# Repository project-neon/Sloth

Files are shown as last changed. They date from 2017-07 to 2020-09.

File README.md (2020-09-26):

# Sloth
The Neon's Line Follower Robot of 2017
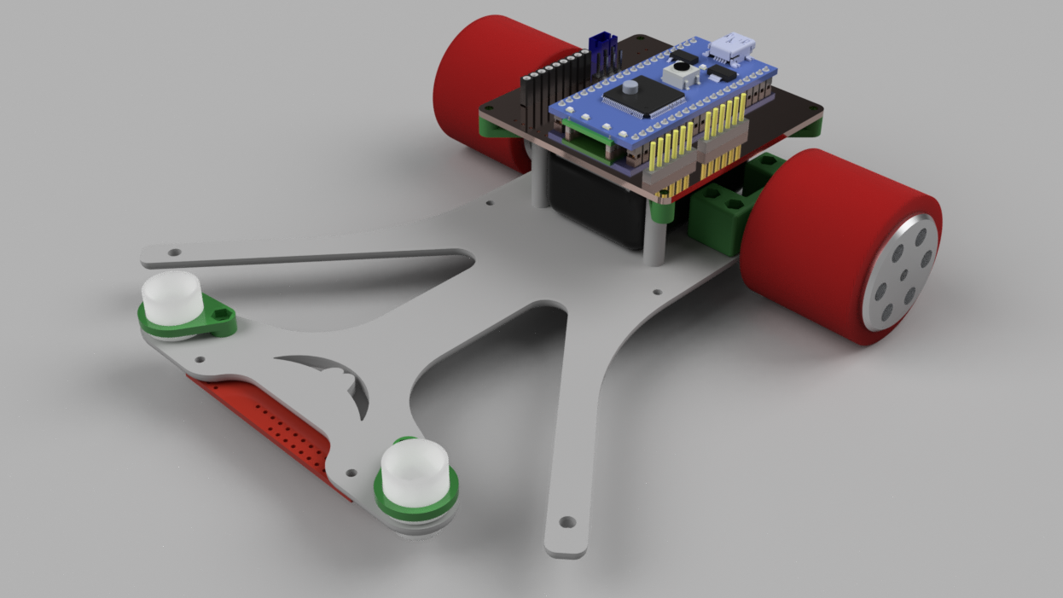
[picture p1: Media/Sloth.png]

<p align="center";> <b>The <strike>slowest</strike> fastest line follower in the ice age.</b> </p>

# Parts of the puzzle
* `Firmware`: Is the main firmware that controls all the functions of the robot.
* `Software`: Is telemetry software for data acquisition from the robot.
* `Eletronics`: This keeps all the information about the electronics for the line following robot ‘NoFollow’.
* `Mechanics`: Contains the STL files of the robot design.

## Firmware
The firmware project was based on the [mbed](https://developer.mbed.org/) development platform and was developed in the [Atom Text Editor](https://atom.io/) equipped with the [Platformio Extension](http://docs.platformio.org/en/latest/ide/atom.html).

### Firmware parts overview
* `main`: Controls all functions of the robot.
* `lineReader`: Read the outside sensors and check the conditions.
* `Motor`: Library for control the power and direction of the motors.
* `PID`: Configures PID control on the angular velocity of the robot.
* `QEI`: Libary for read the magnetic encoders. Available [here](https://developer.mbed.org/cookbook/QEI)
* `QTRSensors`: Library for read the line sensors. Available [here](https://developer.mbed.org/users/phillippsm/code/PololuQTRSensors/).

## Eletronics
The eletronic board was developed in the [Circuit Maker](https://circuitmaker.com/), a PCB Design Freeware. Project available [here](https://circuitmaker.com/Projects/Details/Neon-Project/NeoFollow).

### Bill of materials
| Qtd | Item | Buy | US$ |
|-----|---|-----|-----|
| 1 | ARM mbed NXP LPC1768 Development Board | [World](https://www.pololu.com/product/2150) | 49.00 | 
| 1 | QTR-8A Reflectance Sensor Array | [World](https://www.pololu.com/product/960) | 9.95 | 
| 1 | TB6612FNG Dual Motor Driver Carrier | [World](https://www.pololu.com/product/713) | 4.95 | 
| 1 | Bluetooth Module HC-05 | [World](https://www.robocore.net/loja/produtos/modulo-bluetooth-hc-05.html) | 12.30 | 
| 2 | 30:1 Micro Metal Gearmotor HP 6V with Extended Motor Shaft | [World](https://www.pololu.com/product/2212) | 16.95 | 
| 1 | Magnetic Encoder Pair Kit for Micro Metal Gearmotors | [World](https://www.pololu.com/product/3081) | 8.95 | 
| 1 | Profuse 2S 7.4V 850 Mah LiPo Battery | [World](http://www.jsumo.com/profuse-2s-74v-850-mah-lipo-battery) | 13.50 | 

## Mecanichs
The mechanics project was developed in the [Fusion 360](https://www.autodesk.com/products/fusion-360/overview), a 3D CAD/CAM Software free for students. Project available [here](http://a360.co/2tWd5yP).

### 3D Printed Parts
| Qtd | Item | 
|-----|---|
| 1 | Chassis |
| 4 | Motor Support |
| 2 | Ball Caster Holder |
| 3 | Spacer |
| 1 | PCB Support |

### Bill of materials
| Qtd | Item | Buy | US$ |
|-----|---|-----|-----|
| 1 | Atom Wheel 37x34mm Pair | [World](http://www.jsumo.com/atom-wheel-37x34mm-pair) | 19.50 | 
| 1 | Mini Plastic Caster Wheel Pair | [World](http://www.jsumo.com/mini-plastic-caster-wheel-pair) | 1.40 | 

## Software
Only a concept.

# Contributors
* [Gustavo Silva de Paula](https://github.com/gustavosdepaula)
* [Marcelo Farias](https://github.com/marcelojrfarias)

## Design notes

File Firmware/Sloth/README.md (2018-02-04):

# Sloth
This are the Firmwares used in the Winter Challenge XIII.

Using encoders to map the track to obtain maximum speed on the straight lines and differents PID constants.

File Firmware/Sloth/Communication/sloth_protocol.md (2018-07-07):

# Protocolo de configuração do Sloth

## Estrutura base de comandos

Os comandos podem ter basicamente 5 componentes essenciais, listados abaixo

| Length | Command | Status | Payload | CRC|
| --- | ---  | --- | --- | -- |

- Length: Tamanho do pacote, assim sabemos quantos bytes devemos esperar na serial. É importante considerar que os bytes não chegarão de uma só vez.
- Command: O comando que será recebido e processado
- Status: O status é aplicável à resposta ao comando. É bom ter um ACK pra ter certeza que um comando foi recebido. Mas é dispensável, podemos fazer uma comunicação malha aberta
- Payload: Quando aplicável, o comando poderá possuir um payload, que são dados necessários para o funcionamento do comando (e.g. definição de um valor)
- CRC: Falhas de comunicação acontecem. Esse campo é dispensável a priori, mas talvez a gente precise caso a comunicação esteja muito ruim.

## Lista de comandos

|Comando | OPCODE | TAG| Descrição|
| -----  | --- | --- | --- |
| Increment | 0x21 | SLOTH_OPCODE_INC | Incrementa uma variável utilizada no controle (KP, KI, KD, etc) |
| Decrement | 0x22 | SLOTH_OPCODE_DEC | Decrementa a mesma coisa|
| Set | 0x23 | SLOTH_OPCODE_SET | Define um valor específico para as variáveis utilizadas no controle |
| Full config | 0x24 | SLOTH_OPCODE_CONFIG | Define um conjunto de valores: kp, ki e kd ao mesmo tempo |
| Start | 0x25 | SLOTH_OPCODE_START | Inicia algum ciclo no robô |
| Stop | 0x26 | SLOTH_OPCODE_STOP | Para o que o robô está fazendo |
| Save | 0x27 | SLOTH_OPCODE_SAVE | Salva os parâmetros do PID na EEPROM |

## Definições de Payloads

### Sloth Control Var

Os comandos: Increment, Decrement e Set possuem um payload determinado "variable", uma estrutura de dados que possui um código pra variável e um valor, que define qual variável ele irá modificar. Atualmente, há uma lista com as seguintes variáveis identificadas na lista a seguir:

| Variável | Código | Tag |
| ---  |  ----- | --- |
| KP 	| 0x21 | SLOT_VAR_KP |
| KI 	| 0x22 | SLOT_VAR_KI |
| KD 	| 0x23 | SLOT_VAR_KD |

Exemplos de comandos codificados

| Comando | Byte array | obs|
| ---- | ---- | -- |
| Inc KP | 0x02 0x21 0x21 | Observe que o campo "value" não é preenchido/transmitido |
| Dec KP | 0x02 0x22 0x21 | Observe que o campo "value" não é preenchido/transmitido |
| Dec KD | 0x02 0x22 0x23 | Observe que o campo "value" não é preenchido/transmitido |
| Set KI | 0x06 0x23 0x22 0x00 0x00 0x25 0x31 | Depois temos que ver como fica o endian disso aqui! |
| Set KD | 0x06 0x23 0x23 0x00 0x00 0x02 0x15 | Depois temos que ver como fica o endian disso aqui! |

### Config

O comando de configuração receve uma estrutura de dados do tipo "slot_config_t" que possui valores definidos para kp, ki e kd.

### Exemplo
Os comandos Increment e Decrement podem possuir o seguinte payload: KP, KI ou KD. Numa "metalinguagem" o comando ficaria algo do tipo (excluindo crc):

Requisição:

|2 | Increment | KP |
| -----  | --- | --- |

Resposta:

|2 | Increment | SUCCESS |
| -----  | --- | --- |

O comando Set poderia ter um conjunto de argumentos:

Requisição:

|4 | Set | KP Value | KI Value | KD Value |
| -----  | -- | ---- | --- | --- |

Resposta:

|2 | Set | SUCCESS |
| -----  | --- | --- |

No caso, tudo que vem depois do SET é o payload do comando.

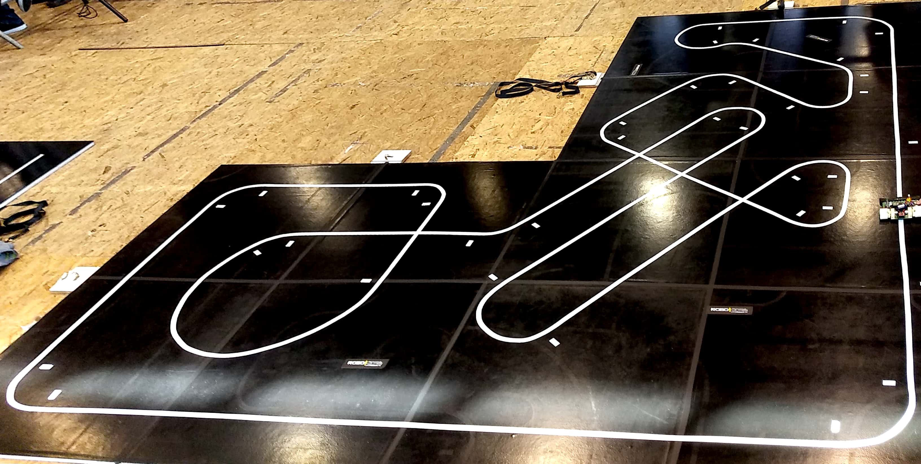
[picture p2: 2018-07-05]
Media/WC14.jpg

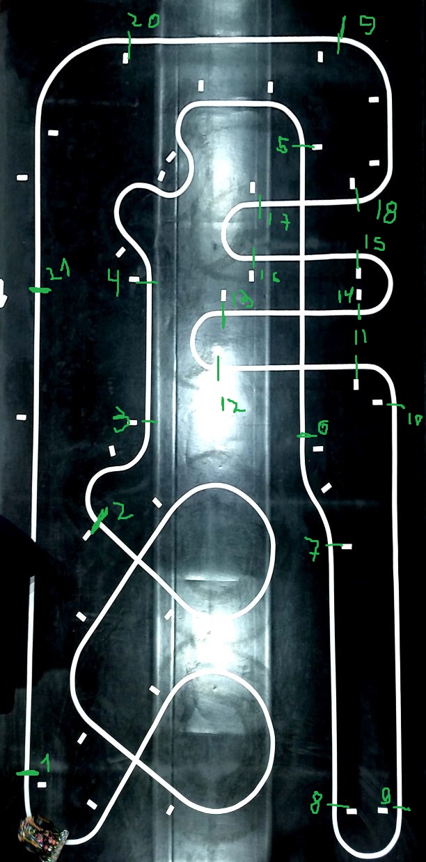
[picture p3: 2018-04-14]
Media/IronCup2018 - Marked.jpg

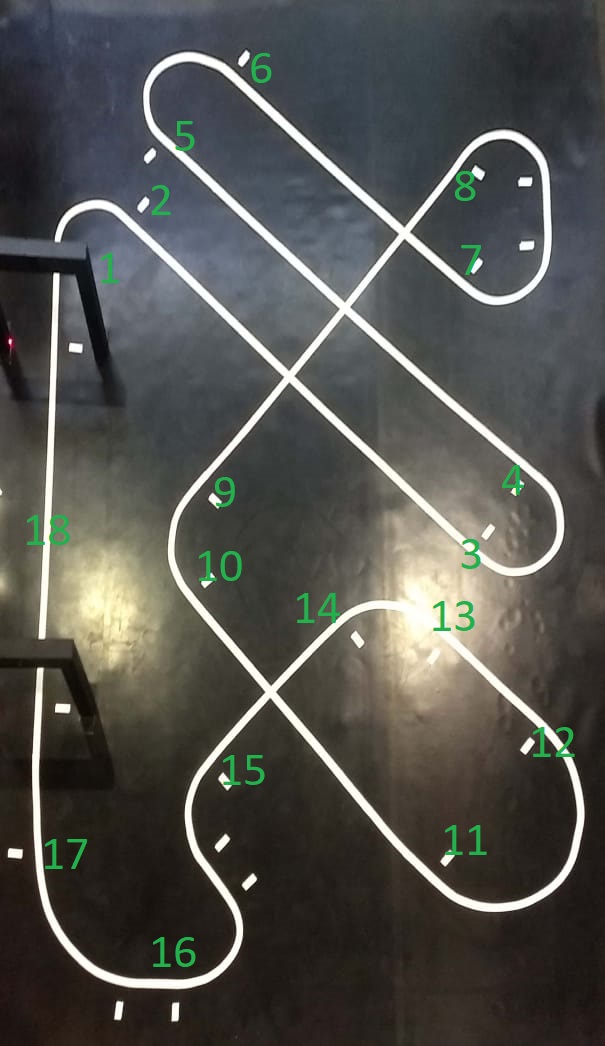
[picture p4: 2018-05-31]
Media/Smile2018 -marked.jpeg

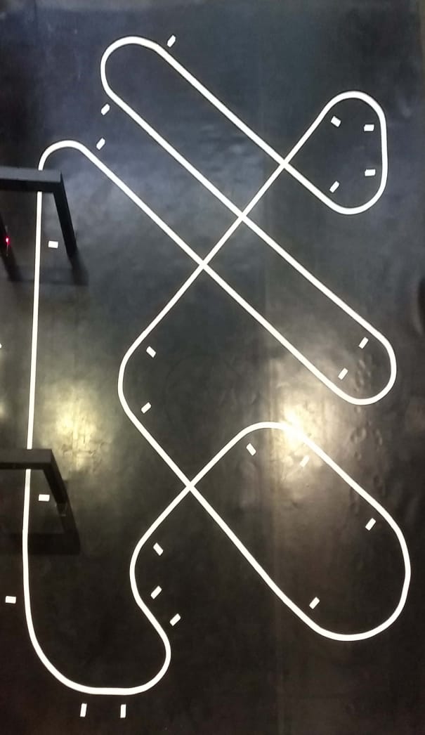
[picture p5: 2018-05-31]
Media/Smile2018.jpeg

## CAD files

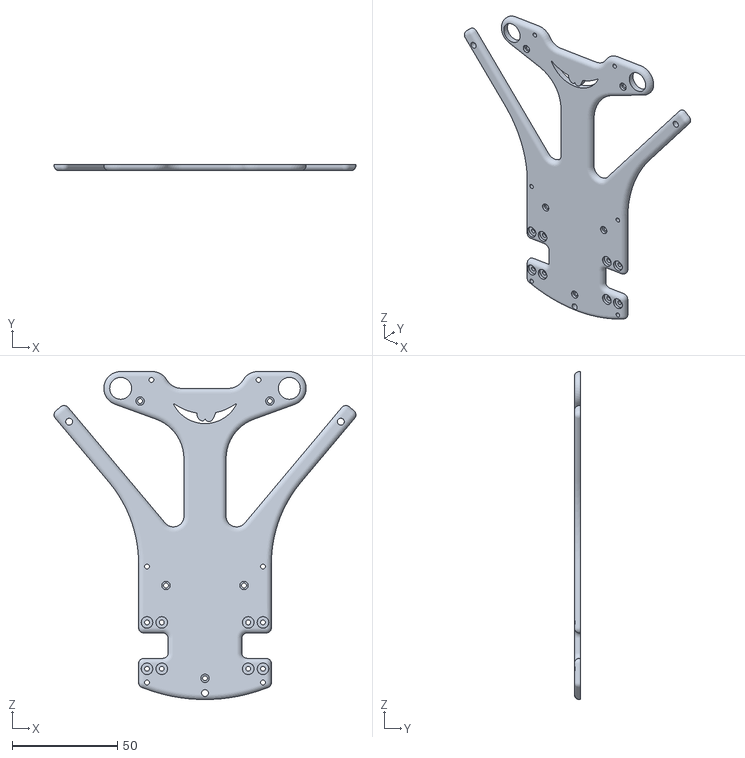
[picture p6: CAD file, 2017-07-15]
Mechanics/STL Files/1x Chassi v26.stl
143.2 x 3.00 x 155.6

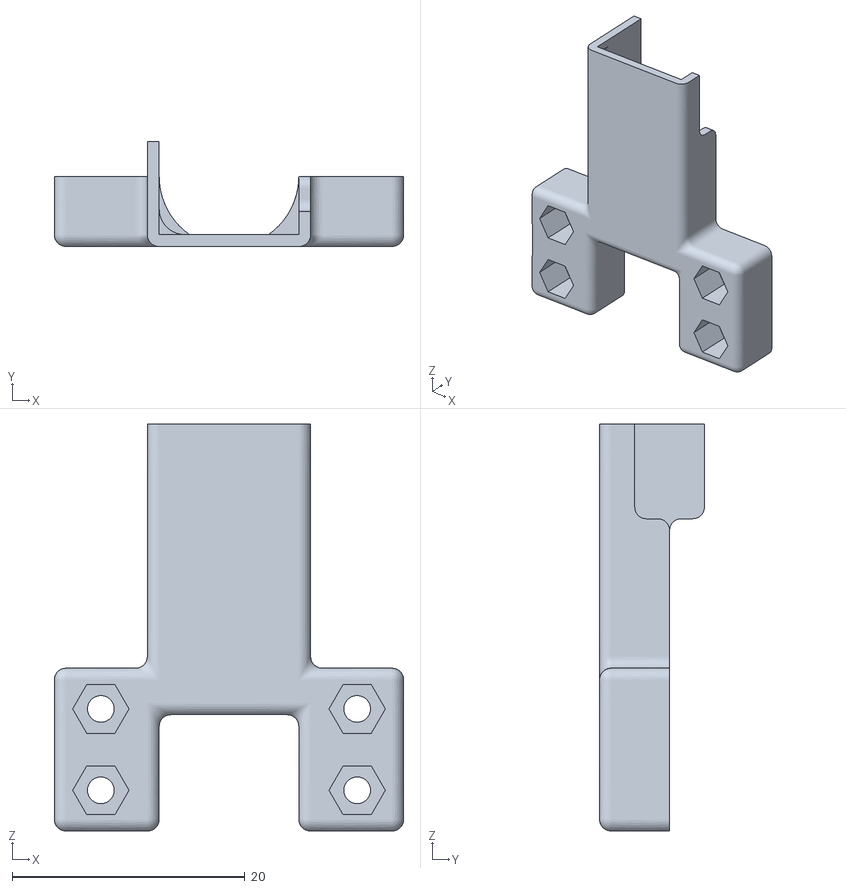
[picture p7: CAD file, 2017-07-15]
Mechanics/STL Files/4x Motor Support v5.stl
30.0 x 9.02 x 35.0

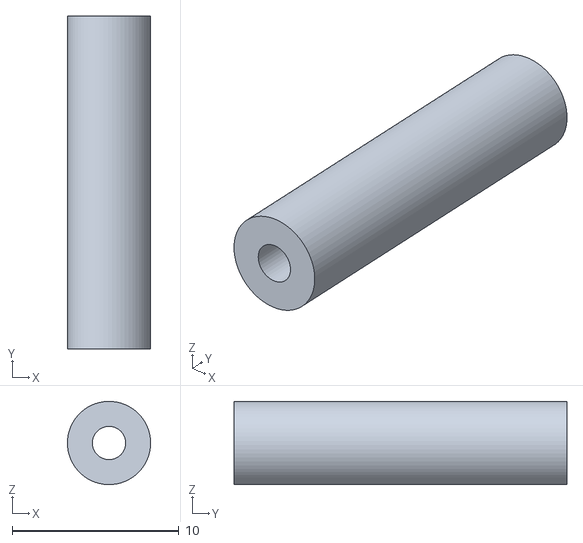
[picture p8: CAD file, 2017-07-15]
Mechanics/STL Files/3x Spacer v7.stl
5.00 x 20.0 x 5.00

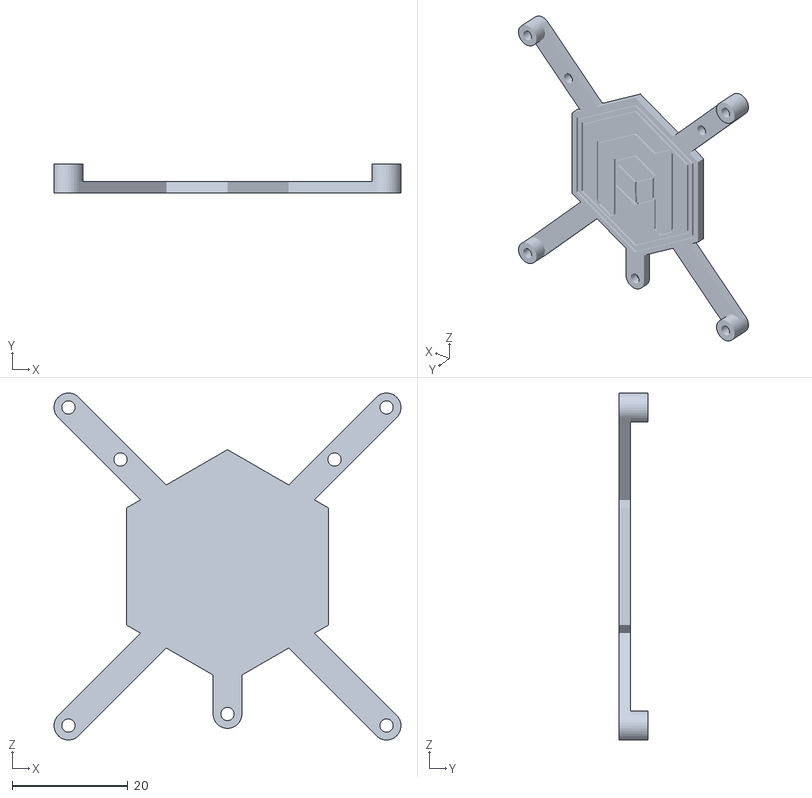
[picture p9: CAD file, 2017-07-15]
Mechanics/STL Files/1x PCBSupport v3.stl
60.0 x 5.00 x 60.0

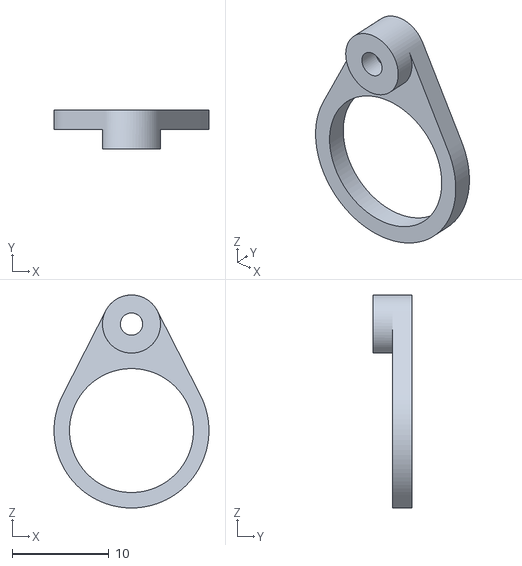
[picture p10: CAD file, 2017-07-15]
Mechanics/STL Files/2x BallCasterHolder v6.stl
16.0 x 4.00 x 22.0

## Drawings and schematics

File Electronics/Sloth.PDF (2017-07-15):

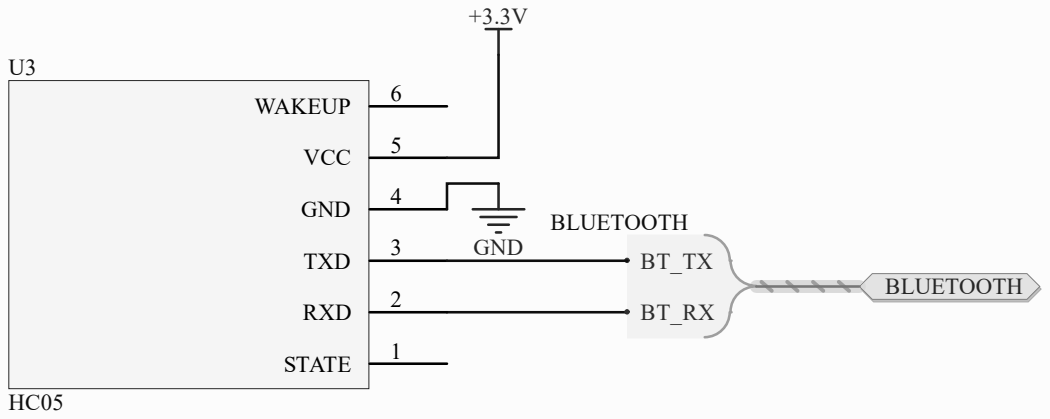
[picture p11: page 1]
POBLUETOOTH0BT0RX POBLUETOOTH0BT0TX

Size A | Number | Revision

Date: 15-Jul-17 | Sheet of
File: Communcation.SchDoc | Drawn By:

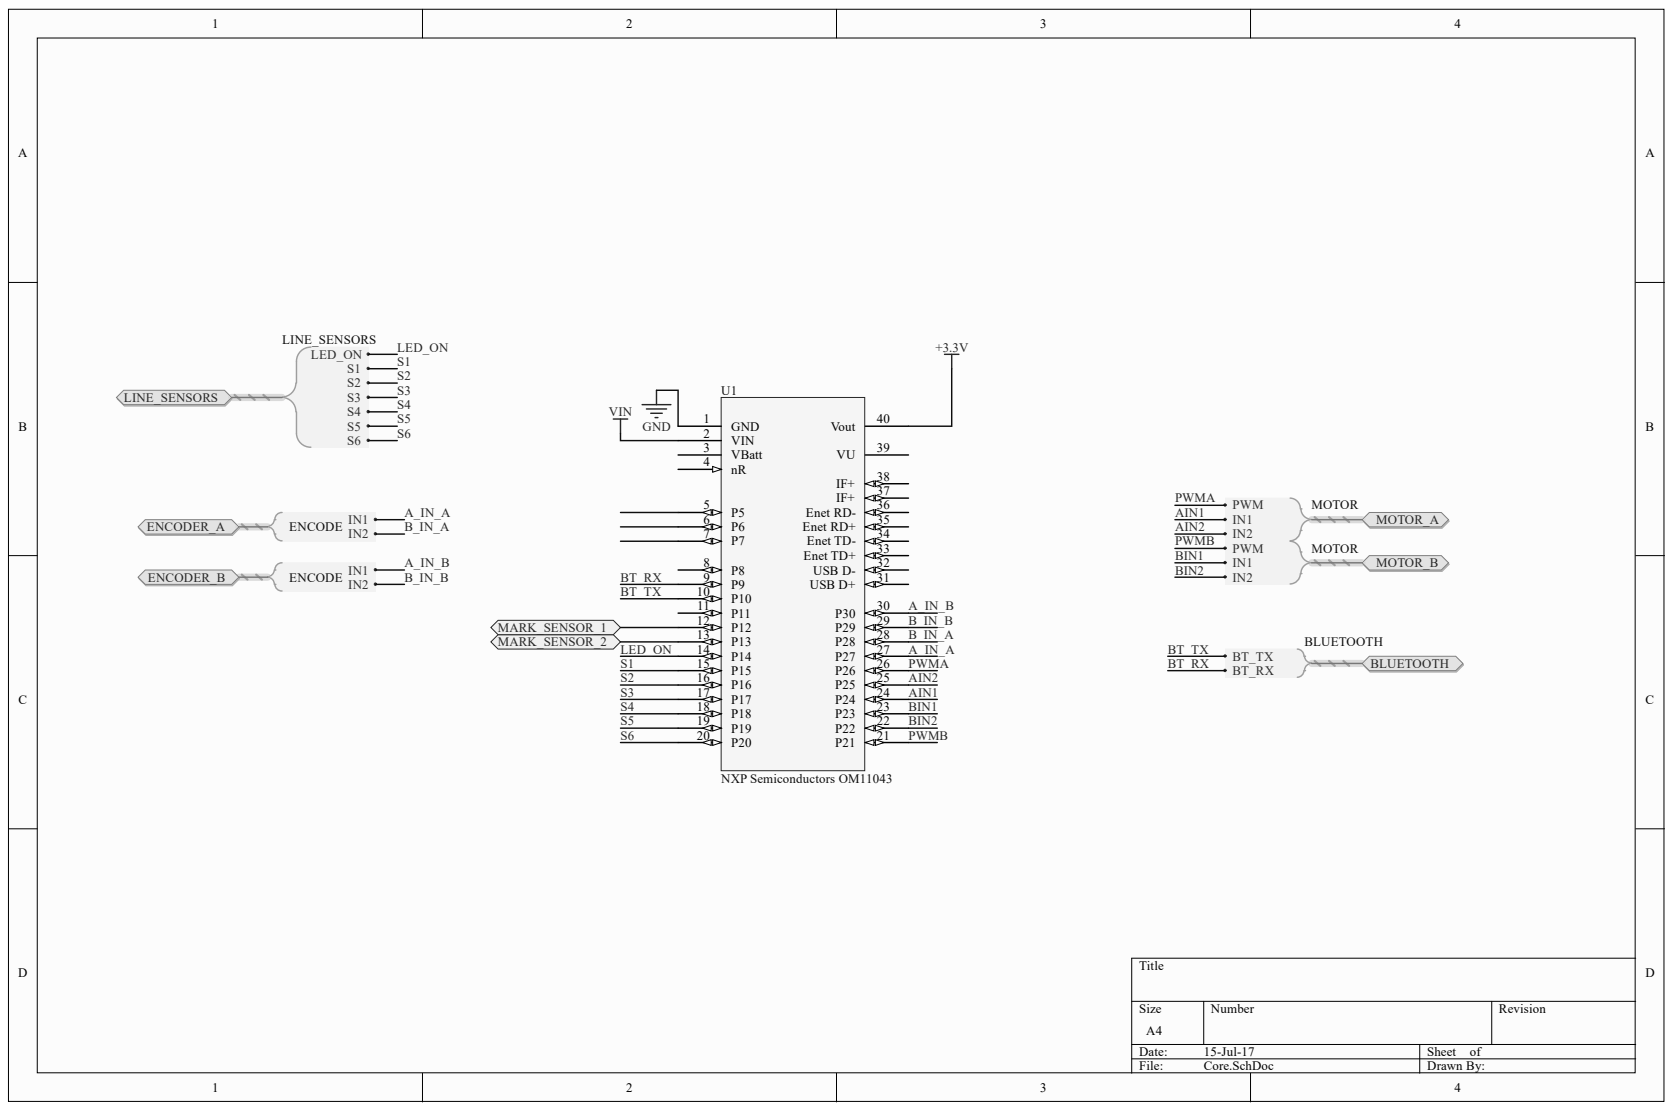
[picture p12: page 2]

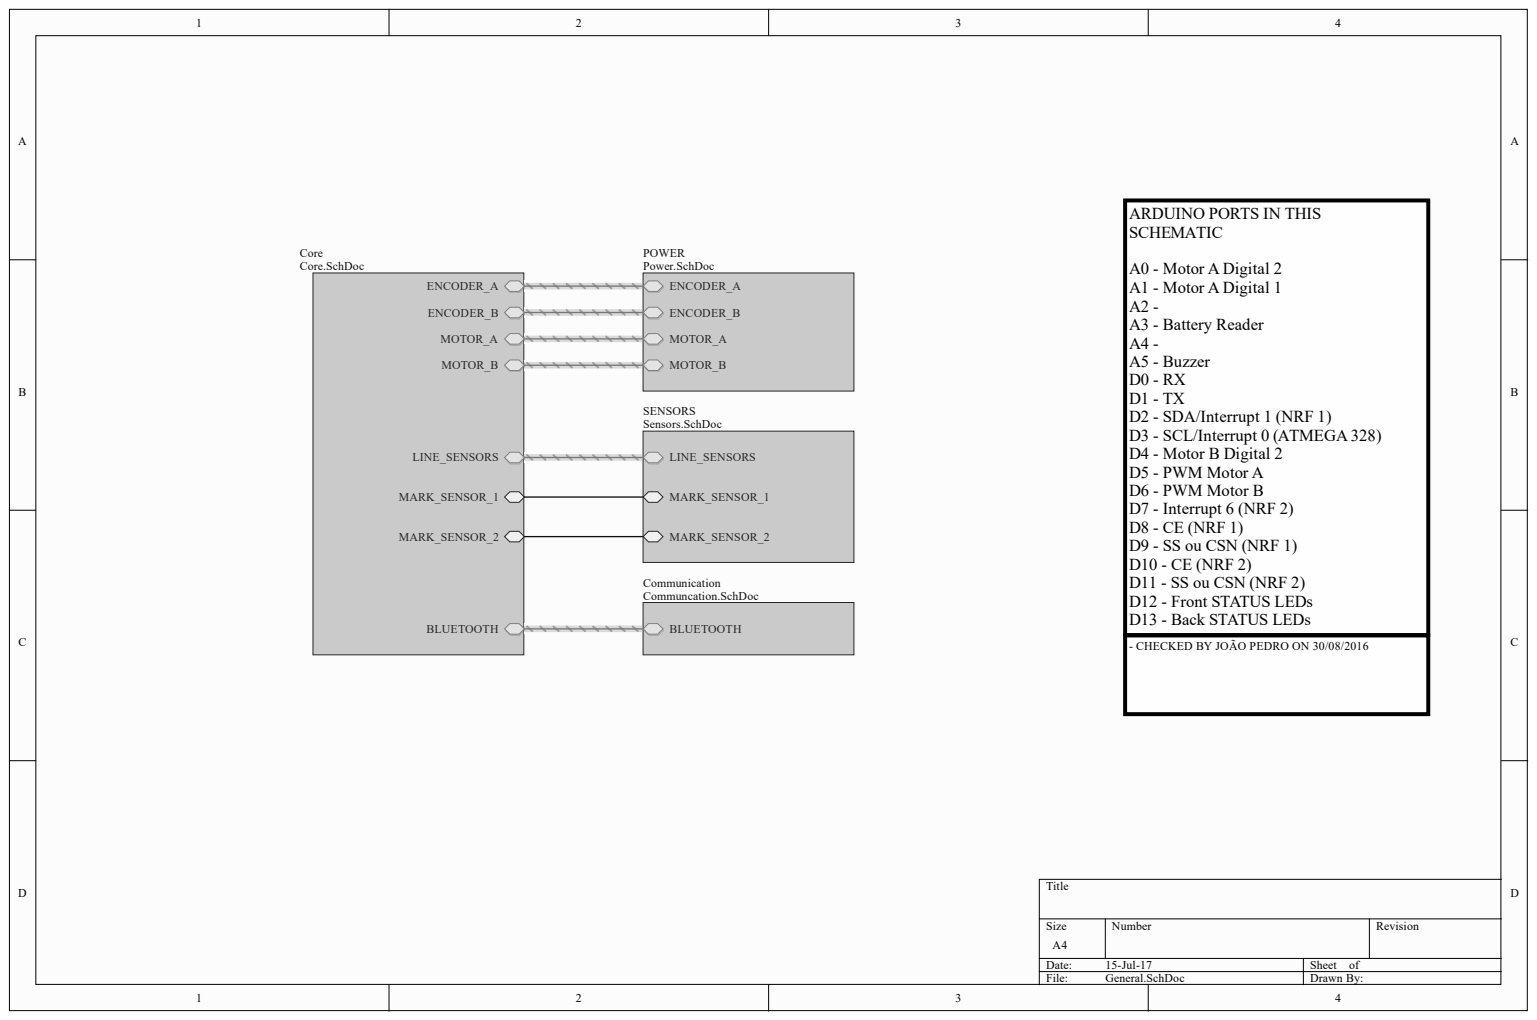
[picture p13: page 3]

ARDUINO PORTS IN THIS
SCHEMATIC

A0 - Motor A Digital 2
A1 - Motor A Digital 1
A3 - Battery Reader
A5 - Buzzer
D2 - SDA/Interrupt 1 (NRF 1)
D3 - SCL/Interrupt 0 (ATMEGA 328)
D4 - Motor B Digital 2
D5 - PWM Motor A
D6 - PWM Motor B
D7 - Interrupt 6 (NRF 2)
D8 - CE (NRF 1)
D9 - SS ou CSN (NRF 1)
D10 - CE (NRF 2)
D11 - SS ou CSN (NRF 2)
D12 - Front STATUS LEDs
D13 - Back STATUS LEDs

- CHECKED BY JOÃO PEDRO ON 30/08/2016

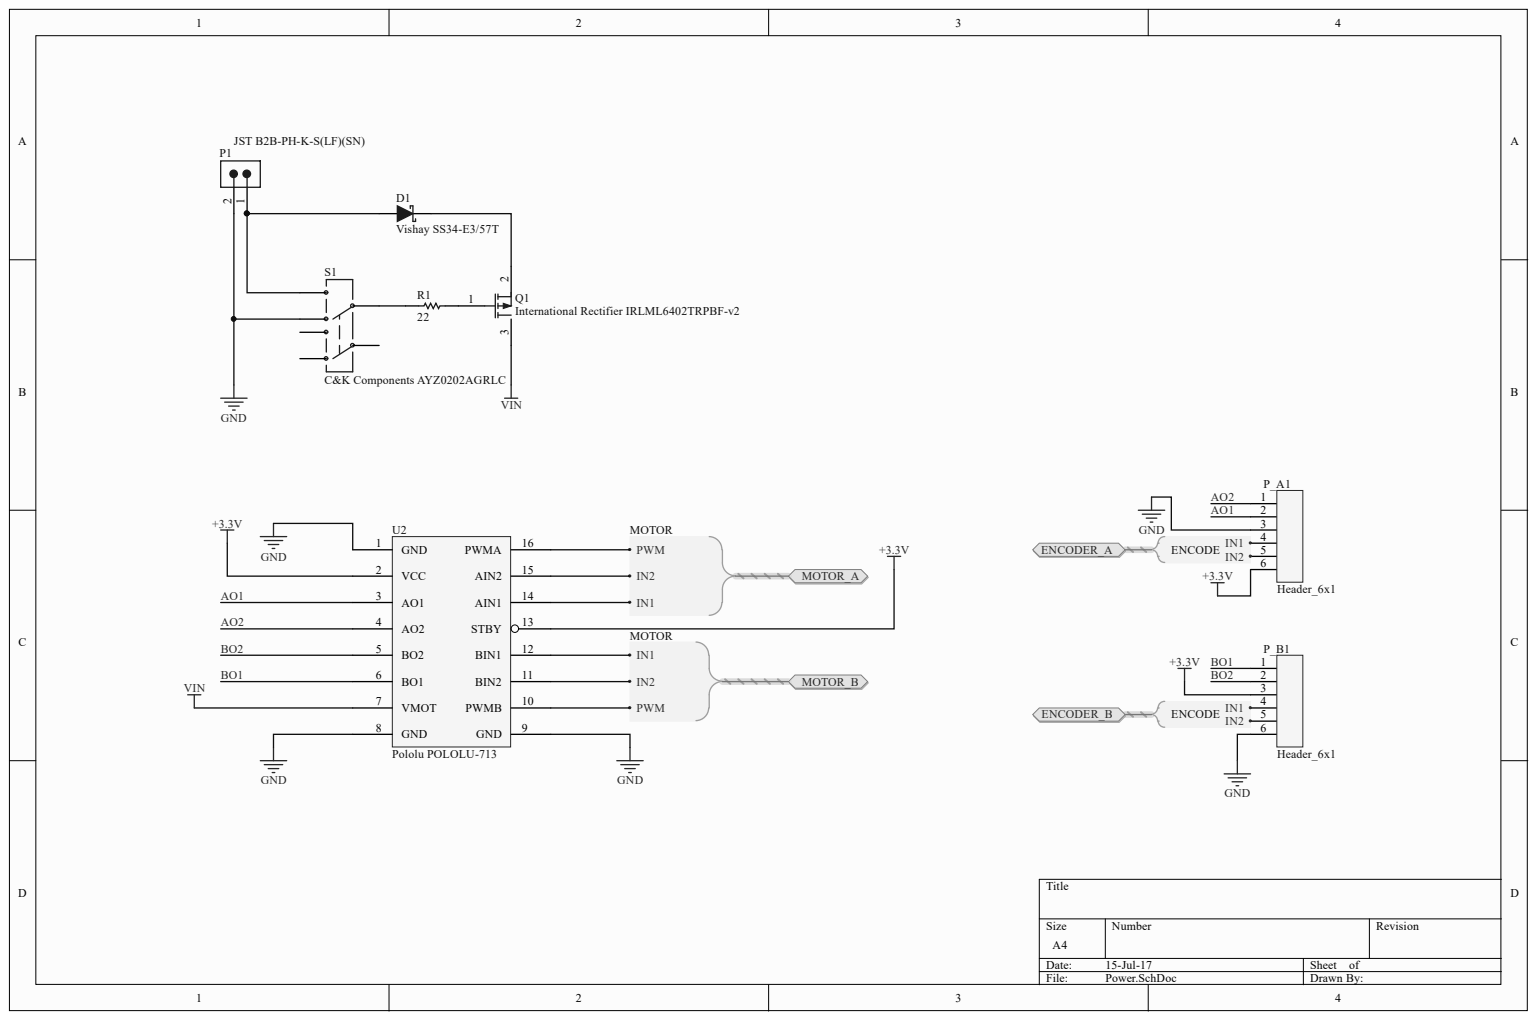
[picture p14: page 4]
File:; Power.SchDoc; Drawn By:; GND 1; VCC 2; VMOT 7; GND 8; GND; Pololu POLOLU-713; C&K Components AYZ0202AGRLC; International Rectifier IRLML6402TRPBF-v2; Vishay SS34-E3/57T; IN1 ENCODE; IN1 ENCODER_B; ENCODE

JST B2B-PH-K-S(LF)(SN)

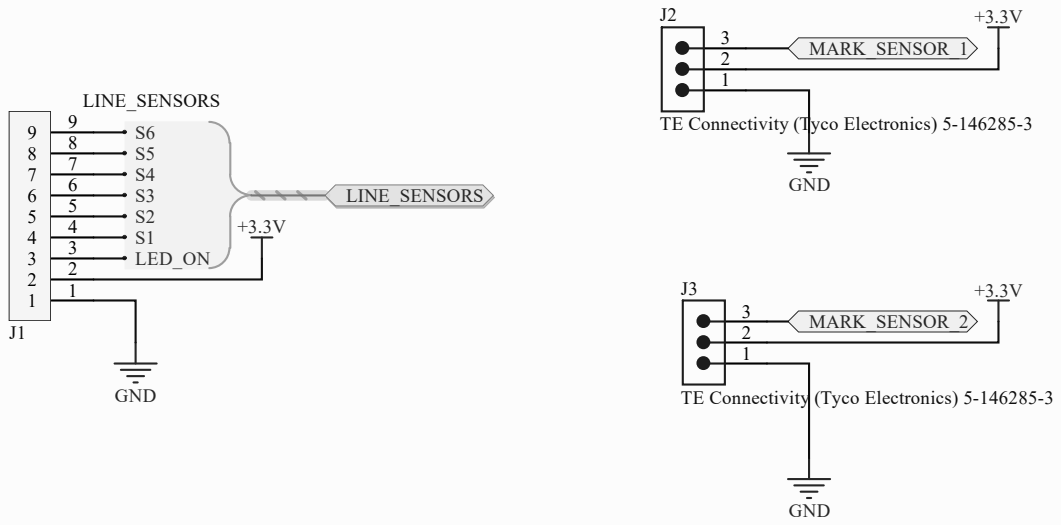
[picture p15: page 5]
File:; Sensors.SchDoc; Drawn By:; TE Connectivity (Tyco Electronics) 5-146285-3; COJ3 PIJ102; PIJ303 POMARK0SENSOR02; POLINE0SENSORS0LED0ON POLINE0SENSORS0S1 POLINE0SENSORS0S2 POLINE0SENSORS0S3 POLINE0SENSORS0S4 POLINE0SENSORS0S5 POLINE0SENSORS0S6

TE Connectivity (Tyco Electronics) 5-146285-3

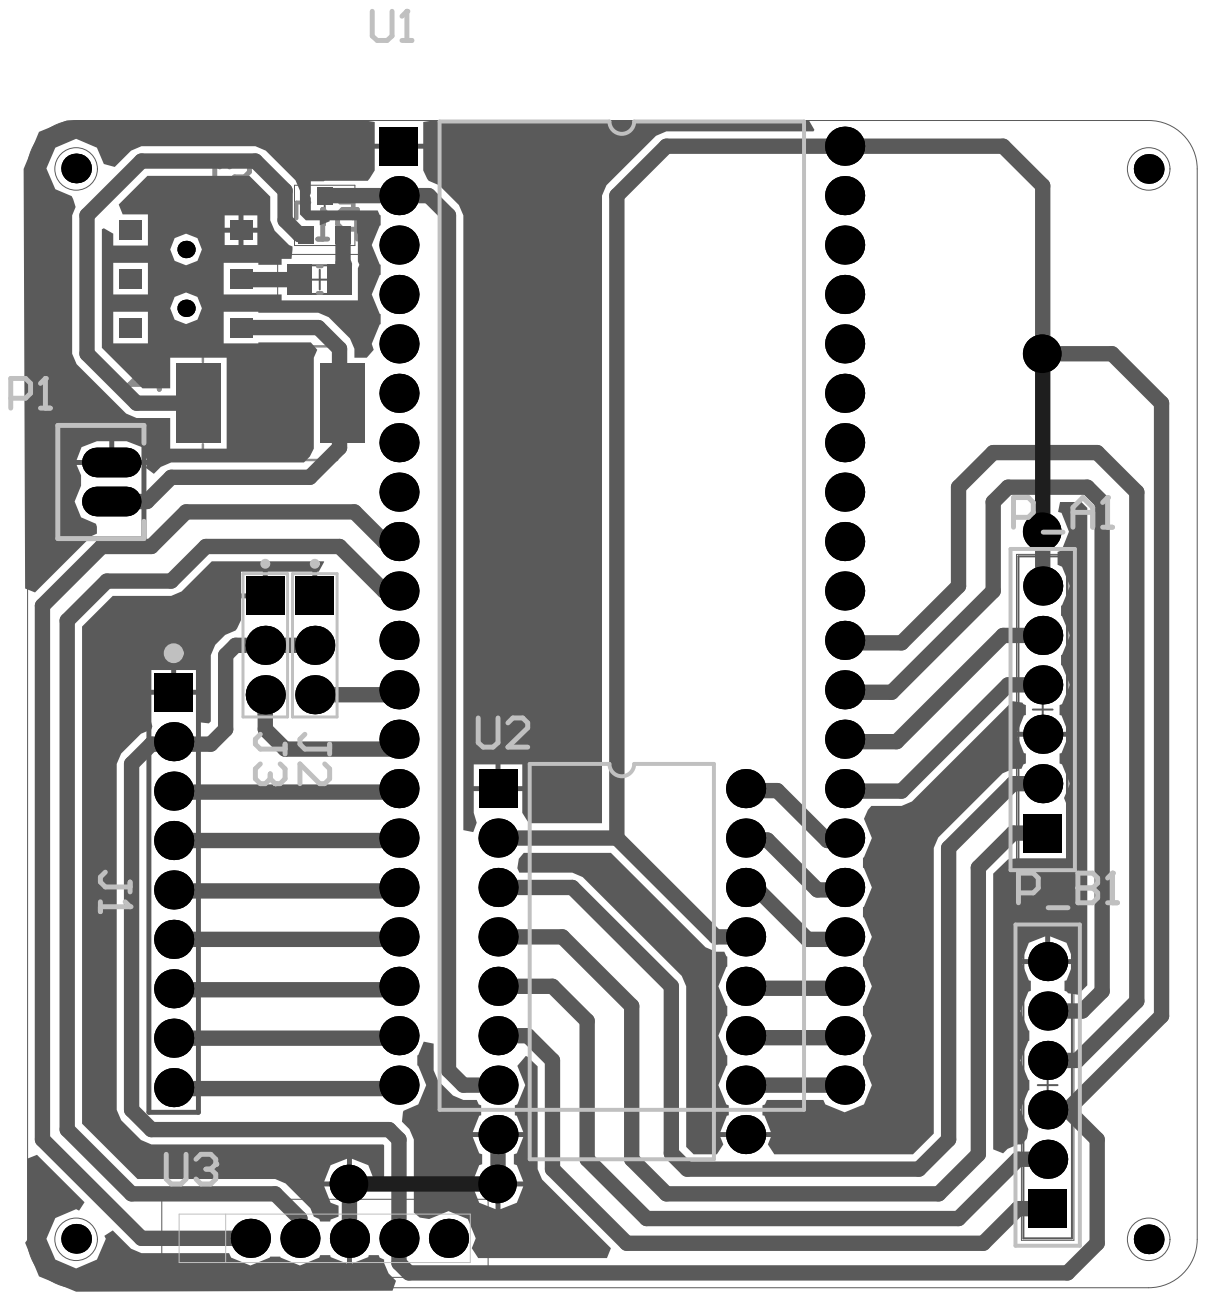
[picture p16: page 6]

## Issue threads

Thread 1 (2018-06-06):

Criar protocolo de comunicação bluetooth para o robô

gabriel-ns, 2018-06-06:
Elaboração de um protocolo de comunicação para o robô ser configurável via bluetooth através de um app ou computador.

Deve-se configurar os parâmetros de controle por enquanto

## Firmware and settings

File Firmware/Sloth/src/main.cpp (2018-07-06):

#include "Motor.h"
#include "QTRSensors.h"
#include "PID.h"
#include "QEI.h"
#include "_config.h"
#include "tracks.h"
// #include "settingsSpeed.h"


// Timers
Timer LogTimer; // Debug the loop
Timer LapTimer; // Time of a lap
Timer AccTimer; // Acceleration interval
Timer cps_left_led_timer; // Acceleration interval
Timer cps_right_led_timer; // Acceleration interval

// Serial
//Control the Communication with a Computer (Serial) and HC-05
Serial PC(USBTX, USBRX);
Serial BT(BTRX, BTTX);

// Leds
DigitalOut leds[4] = {
    LED1,
    LED2,
    LED3,
    LED4
};

// Motors
Motor LeftMotor(PIN_M1_EN, PIN_M1_IN1, PIN_M1_IN2); // Lefut Motor
Motor RightMotor(PIN_M2_EN, PIN_M2_IN1, PIN_M2_IN2); // Right Motor
float leftmotorspeed = 0.0;
float righmotorspeed = 0.0;
float currentSpeed = 0.0;
float targetSpeed = 0.0;
float acceleration = 0.0;

// Encoders
QEI LeftEncoder (PIN_ENC1_A, PIN_ENC1_B, NC, PULSES_PER_REV); // Left Encoder
QEI RightEncoder (PIN_ENC2_A, PIN_ENC2_B, NC, PULSES_PER_REV); // Right Encoder
float currentPosition; // Robot current position in the track
float leftDistance; // left distance by encoder (m)
float rightDistance; // right distance by encoder (m)

bool firstMarkDone = false;

float POSITION_FIX = 0; //Robot constante to fix the position.

// Line Reader
PinName pinsLineReader[NUM_SENSORS] = {
    PIN_LR_S0, // Most Left Sensor
    PIN_LR_S1,
    PIN_LR_S2,
    PIN_LR_S3,
    PIN_LR_S4,
    PIN_LR_S5 // Most Right Sensor
};
QTRSensorsAnalog LineReader(pinsLineReader,
    NUM_SENSORS, NUM_SAMPLES_PER_SENSOR, EMITTER_PIN);
unsigned int sensorvalues[NUM_SENSORS];
int linePosition; // line position in the line reader

// Lap sensor settings
InterruptIn CheckpointSensorRight(PIN_TRACK_MARKING_RIGHT);
InterruptIn CheckpointSensorLeft(PIN_TRACK_MARKING_LEFT);

// Counters of left and Right sensors
int checkpoint_left_counter = 0;
int checkpoint_right_counter = 0;
int last_checkpoint_left_counter = 0;
int last_checkpoint_right_counter = 0;
int crossroad_counter = 0;

bool robotstate = true;
bool readyStatus = true;
bool motorsEnable=true;

//PID
float directiongain = 0.0;
PID directioncontrol(0, 0, 0);


// float speedbase = 0.30;
// float kpdir = 0.00020;
// float kidir = 0.000000;
// float kddir = 0.0000035;

float speedbase = 0.85;
float kpdir = 0.00022;
float kidir = 0.0000000;
float kddir = 0.000015;

Setup Normal     = {speedbase, kpdir, kidir, kddir};

void setRobotSetup(Setup setup) {
  // Setup PID and Speed
  targetSpeed = setup.speed;
  directioncontrol.setTunings(setup.kp, setup.ki, setup.kd);
  // If line position is 0, the robot is just over the line
  directioncontrol.setSetPoint(0);
}

// The target mark
Mark TargetMark;
int currentMark = 0;

// Function to calibrate the line reader
void lineReaderCalibrate() {

  PC.printf("%s", "Calibrating sensors...");
  BT.printf("%s", "Calibrating sensors...");
  leds[0] = 1;
  for (int i = 0; i < 1000; i++)
    LineReader.calibrate(true);
  leds[0] = 0;
  BT.printf("%s\n", "Done.");
  PC.printf("%s\n", "Done.");
  //
  // for (int i = 0; i < NUM_SENSORS; i++)
  //   LOG.printf("Min: %4i \t", LineReader.calibratedMinimumOn[i]);
  //
  // LOG.printf("%s", "\n");
  //
  // for (int i = 0; i < NUM_SENSORS; i++)
  //   LOG.printf("Max: %4i \t", LineReader.calibratedMaximumOn[i]);

  // LOG.printf("%s", "\n");
  // LOG.printf("%s", "\n");
}

void btcallback() {
  char rcvd = BT.getc();
  switch (rcvd) {
    case 'A':
      kpdir += 0.00005;
      break;
    case 'B':
      kpdir -= 0.00005;
      break;
    case 'C':
      kidir += 0.0000001;
      break;
    case 'D':
      kidir -= 0.0000001;
      break;
    case 'E':
      kddir += 0.000005;
      break;
    case 'F':
      kddir -= 0.000005;
      break;
    case 'u':
      speedbase += 0.01;
      break;
    case 'd':
      speedbase -= 0.01;
      break;
    // case 'S':
    //   robotstate = false;
    //   break;
    case 'J':
      PC.printf("Encoder Right Now: %.0f \n", currentPosition);
      BT.printf("Encoder Right Now: %.0f \n", currentPosition);
      break;
    case 'G':
      robotstate = true;
      // robotstate = true;
      PC.printf("Robot will Start in 2s");
      BT.printf("Robot will Start in 2s");
      LeftEncoder.reset();
      RightEncoder.reset();
      wait(2);
      break;
    case 'S':
      robotstate = false;
      // robotstate = true;
      PC.printf("Robot Paused");
      BT.printf("Robot Paused");
      break;
    case 'M':
      motorsEnable = !motorsEnable;
      // robotstate = true;
      PC.printf("Motors state changed");
      BT.printf("Motors state changed");
      break;
  }
   directioncontrol.setTunings(kpdir, kidir, kddir);
   BT.printf("%.8f %.8f %.2f\n", kpdir, kddir, speedbase);
}

// Interrupt when Mark Left was change
void checkpointSensorLeftCallback() {
    checkpoint_left_counter++;
    cps_left_led_timer.start();
    leds[0] = 1;
}

//Interrupt when Mark Right was change
void checkpointSensorRightCallback() {
    checkpoint_right_counter++;
    cps_right_led_timer.start();
    leds[3] = 1;
}

int main() {

  // Setup Serial and Welcome message
  PC.baud(PC_SPEED);
  BT.baud(BT_SPEED);
  BT.attach(&btcallback);
  BT.printf("%s ", PROJECT_NAME); LOG.printf("%s\n", PROJECT_VERSION);
  PC.printf("%s ", PROJECT_NAME); LOG.printf("%s\n", PROJECT_VERSION);

  // Release motors for make more easy the calibration
  LeftMotor.coast();
  RightMotor.coast();

  // Calibrate the line sensor
  wait(2);
  lineReaderCalibrate();
  wait(4);

  // Reset Encoders
  LeftEncoder.reset();
  RightEncoder.reset();

  // Activating Interrupt in fall for the Mark Sensors
  CheckpointSensorRight.fall(&checkpointSensorRightCallback);
  CheckpointSensorLeft.fall(&checkpointSensorLeftCallback);

  // Clear mark sensors counters
  checkpoint_left_counter = 0;
  checkpoint_right_counter = 0;

  // Start Timers
  LogTimer.start();
  LapTimer.start();
  AccTimer.start();

  // Set the first setup of the Robot
  if(MAPPING_ENABLED){
    // Get first target mark - 0
    TargetMark = TRACK_EVENT_NAME[currentMark];
    acceleration = TargetMark.acceleration;
    // Update Robot Setup
    setRobotSetup(TargetMark.setup);
  } else {
    // Get first target mark - 0
    TargetMark = TRACK_EVENT_NAME[currentMark];
    acceleration = TargetMark.acceleration;
    // Update Robot Setup
    setRobotSetup(Normal);
  }
  // Main Loop
  while(1) {

    // Get currrent position by encoders and convert to meters

    if (checkpoint_right_counter == 0) {
      LeftEncoder.reset();
      RightEncoder.reset();
    }

    leftDistance = PULSES2DISTANCE(LeftEncoder.getPulses());
    rightDistance = PULSES2DISTANCE(RightEncoder.getPulses());
    currentPosition = AVG(leftDistance, rightDistance) + POSITION_FIX; //get average

    // Check if the robot complete the track
    if (currentPosition >= FINAL_TARGET_POSITION && STOP_BY_DISTANCE) {
      robotstate = false; // Stop the Robot
    }

    // Checks if medium lap time has been reached
    if (LapTimer.read() > LAP_TIME && STOP_BY_TIME) {
      LapTimer.stop();
      robotstate = false; // Stop the robot
    }

    // if (currentMark>0)
    //   CheckpointSensorRight.disable_irq();

    if (!robotstate) { // Stop the Robot
      // Stop the robot and release the motors after
      LeftMotor.brake();
      RightMotor.brake();
      wait(.500);
      LeftMotor.coast();
      RightMotor.coast();

      // Stop the Lap Timer
      LapTimer.stop();

      // Print some data for statistics
      float laptime = LapTimer.read();
      float mediumspeed = currentPosition / laptime;
      BT.printf("Time Lap: %.5f\t", laptime);
      BT.printf("Track Length: %.2fm\t ", currentPosition);
      BT.printf("Medium Speed: %.2fm/s\t ",  mediumspeed);
      BT.printf("%s\n", "");

      PC.printf("Time Lap: %.5f\t", laptime);
      PC.printf("Track Length: %.2fm\t ", currentPosition);
      PC.printf("Medium Speed: %.2fm/s\t ",  mediumspeed);
      PC.printf("%s\n", "");

      // Blink the LEDs
      while (!robotstate) {
        for (int i = 0; i <= 3; i++) {
          for (int j = 0; j <= 3; j++) {
            leds[j] = j == i;
            wait(.050);
          }
        }
      }
    }

    else if (robotstate) { // Follow the Line

      //LEDS turn off - About Interrupt
      if (cps_left_led_timer.read() > 0.150) {
        leds[0] = 0;
        cps_left_led_timer.reset();
        cps_left_led_timer.stop();
      }

      if (cps_right_led_timer.read() > 0.150) {
        leds[3] = 0;
        cps_right_led_timer.reset();
        cps_right_led_timer.stop();
      }


      // Check if changed mark
      if (currentPosition >= TargetMark.position && MAPPING_ENABLED) {
        currentMark++;
        // Get current Target Mark
        TargetMark = TRACK_EVENT_NAME[currentMark];
        acceleration = TargetMark.acceleration;
        // Update Robot Setup
        setRobotSetup(TargetMark.setup);
      }

      // Position of the line: (left)-2500 to 2500(right)
      linePosition = LineReader.readLine(sensorvalues, QTR_EMITTERS_ON, WHITE_LINE) - 2500.0;

      directioncontrol.setProcessValue(linePosition);
      directiongain = directioncontrol.compute();

      // Speed update with acceleration
      if (ACCELERATION_ENABLED) {
        if (AccTimer.read() > ACCELERATION_INTERVAL) {
          // check if the robot accelerates or decelerates
          if ((acceleration > 0 && currentSpeed < targetSpeed) || (acceleration < 0 && currentSpeed > targetSpeed)) {
            currentSpeed += acceleration * ACCELERATION_INTERVAL;
            currentSpeed = currentSpeed > targetSpeed ? targetSpeed : currentSpeed < 0.0 ? 0.0 : currentSpeed;
            AccTimer.reset();
          }
        }
      } else {
        currentSpeed = targetSpeed;
      }

      // Set the Direction
      leftmotorspeed = currentSpeed + (directiongain > 0 ? -directiongain : 0);
      righmotorspeed = currentSpeed + (directiongain < 0 ? +directiongain : 0);

      // Constrain the speed value to [0.0, 1.0] interval
      leftmotorspeed = leftmotorspeed > 1.0 ? 1.0 : leftmotorspeed < -REVERSE ? -REVERSE : leftmotorspeed;
      righmotorspeed = righmotorspeed > 1.0 ? 1.0 : righmotorspeed < -REVERSE ? -REVERSE : righmotorspeed;

      // LOG.printf("PID is working? %f \n", directiongain);
      if(motorsEnable){
        LeftMotor.speed(leftmotorspeed);
        RightMotor.speed(righmotorspeed);
      }

    // Test Motors
      // LeftMotor.speed(0.5);
      // RightMotor.speed(0.5);
      // wait(2);
      // LeftMotor.brake();
      // RightMotor.brake();
      // wait(2);
      // LeftMotor.speed(-0.5);
      // RightMotor.speed(-0.5);
      // wait(2);
      // LeftMotor.brake();
      // RightMotor.brake();
      // wait(2);
    }

    if (LogTimer.read() > LOG_INTERVAL && LOG_ENABLED) {
      // LOG.printf("%i\t", currentPosition);
      // LOG.printf("%i\t", TargetMark.position);
      // LOG.printf("%i\t", currentMark);

      // Certifies correct operation of line sensors
      // LineReader.read(sensorvalues, QTR_EMITTERS_ON);
      //  for (int i = 0; i < 6; i++)
      //   LOG.printf("%i \t", sensorvalues[i]);
      // LOG.printf("Line: %i \t", linePosition);

      // LOG.printf("Mark: %i \t", MarksensorTest.read());


     // Certifies correct operation of encoders
     LOG.printf("Left Encoder: %i \t", LeftEncoder.getPulses());
     LOG.printf("Right Encoder: %i \t", RightEncoder.getPulses());
     // LOG.printf("%.4f\t", leftDistance);
     // LOG.printf("%.4f\t", rightDistance);

     // Certifies correct operation of motors
     // LOG.printf("PID is working? %f \n", directiongain);
     // LOG.printf("%.2f\t", leftmotorspeed);
     // LOG.printf("%.2f\t", righmotorspeed);

      // Manual Track Mapping
      // LOG.printf("%.2f,", LapTimer.read());
      // LOG.printf("%i,", currentMark);
      // LOG.printf("%i", linePosition);

      // LOG.printf("%.4f,", currentPosition);
      // LOG.printf("%.4f", DIF(leftDistance, rightDistance));
/*
      // Checkpoint sensors mapping
      // Crossroad
      if (checkpoint_left_counter != last_checkpoint_left_counter && checkpoint_right_counter != last_checkpoint_right_counter) {
        crossroad_counter++;
        LOG.printf("%s,%i,", "C", crossroad_counter);
        checkpoint_left_counter--;
        checkpoint_right_counter--;
      }
      // Curve start/end marks
      else if (checkpoint_left_counter != last_checkpoint_left_counter && checkpoint_right_counter == last_checkpoint_right_counter) {
        LOG.printf("%s,%i,", "L", checkpoint_left_counter);
        last_checkpoint_left_counter = checkpoint_left_counter;
      }
      // Start/Finish marks
      else if (checkpoint_left_counter == last_checkpoint_left_counter && checkpoint_right_counter != last_checkpoint_right_counter) {
        LOG.printf("%s,%i,", "R", checkpoint_right_counter);
        last_checkpoint_right_counter = checkpoint_right_counter;
      }
      else {
        LOG.printf("%s", "-,-,");
      }

      // Encoders positions
      LOG.printf("%.2f,", leftDistance);
      LOG.printf("%.2f", rightDistance);
*/

      // LOG.printf("%i", checkpoint_right_counter);
      //Test of Mapping
      // LOG.printf("CurrentPosition: %.2f \t", currentPosition);
      // LOG.printf("CurrentSpeed: %.2f \t", TargetMark.setup.speed);

      LOG.printf("%s","\n");
      LogTimer.reset();
    }
  }

}

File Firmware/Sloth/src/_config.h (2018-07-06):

#ifndef CONFIG_H
#define CONFIG_H
#include "mbed.h"

//
// Project
//
#define PROJECT_NAME            "Sloth Firmware"
#define PROJECT_VERSION         "v2.0"

//
// Serial DEBUG
//
#define LOG_ENABLED false
#define LOG if(LOG_ENABLED) BT
#define PC_SPEED  115200
#define LOG_INTERVAL  0.01 //

//
// Bluetooth Configs (Type here)
//
#define BT_SPEED  115200
#define BTRX  p9
#define BTTX  p10

//
// Line Reader Settings
//
#define WHITE_LINE  true
#define NUM_SENSORS 6  // number of sensors used
#define NUM_SAMPLES_PER_SENSOR  1  // average 4 analog samples per sensor reading
#define EMITTER_PIN p14  // emitter is controlled by digital pin 2
#define PIN_LR_S0 p15
#define PIN_LR_S1 p16
#define PIN_LR_S2	p17
#define PIN_LR_S3	p18
#define PIN_LR_S4	p19
#define PIN_LR_S5	p20

//
//Lap Sensor Settings
//
#define CROSS_COUNTER 6
#define PIN_TRACK_MARKING_RIGHT p11
#define PIN_TRACK_MARKING_LEFT  p12

//
// General Settings
//
#define STOP_BY_TIME false
#define LAP_TIME 5 //in seconds
#define STOP_BY_DISTANCE true
#define FINAL_TARGET_POSITION   24.0  // in meters
// #define FINAL_TARGET_POSITION   1.5
#define ACCELERATION_ENABLED true
#define ACCELERATION_INTERVAL 0.01
#define MAPPING_ENABLED true
#define FIRST_MARK_POSITION 0.5

//
//Marking Settings
//

//
// Motors config (H-Bridge)
//
#define REVERSE	0.00
#define PIN_M2_EN   p21
#define PIN_M2_IN1  p22
#define PIN_M2_IN2  p23
#define PIN_M1_EN   p26
#define PIN_M1_IN1  p24
#define PIN_M1_IN2  p25

//
// Encoder config (Quadrature)
//
#define PULSES_PER_REV 179.0 // 30:1
// #define PULSES_PER_REV 61.0 // 10:1
#define PIN_ENC1_A  p27
#define PIN_ENC1_B	p28
#define PIN_ENC2_A	p30
#define PIN_ENC2_B	p29
//#define M_PI 3.14159
#define WHEEL_RADIUS 0.016	// D = 32mm
#define WHEEL_PERIMETER	(2.0*WHEEL_RADIUS*M_PI)	// WHEEL_RADIUS * PI
#define PULSES2DISTANCE(p) (p / PULSES_PER_REV * WHEEL_PERIMETER)
#define AVG(l,r) ((l + r) / 2.0)
#define DIF(l,r) (r - l)
//
// Pulses to Distance
//

#define SlowCurve 0
#define Curve     1
#define FastCurve 2
#define Straight  3
#define Stop      4

#define TRACK_EVENT_NAME WC14_2018_SAFE
#define GAIN_NUMBER k3

#endif

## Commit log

2017-07-15 Electronics and Mechanics files addes
    [1x Chassi v26.stl, 1x PCBSupport v3.stl, 2x BallCasterHolder v6.stl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]
2017-07-15 Update the Sloth image
2017-07-15 Add encoder to biill of materials
2018-02-04 Setup some Flags
    [PID Control.ods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]
2018-02-04 Convert Pulses2Distance for brake robot
2018-02-25 PID control change
2018-07-01 Mark Sensor update
2018-07-02 sensor bug fix
2018-07-04 Checkpoint sensor right tested.
2018-07-04 Track mapping tests.
2018-07-05 Mapping by encoder with the help of checkpoint sensors added.
2018-07-05 Extend the on time of the checkpoint led indicators.
